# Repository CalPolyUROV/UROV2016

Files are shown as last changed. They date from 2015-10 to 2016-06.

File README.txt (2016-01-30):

# UROV_2016 README
#
##################################
#	Useful Links
##################################
#
# Arduino PWM HOW TO
#	https://www.arduino.cc/en/Tutorial/SecretsOfArduinoPWM
#
# Timer Frequency Charts 
#	https://arduino-info.wikispaces.com/Arduino-PWM-Frequency
#
# 9DOF Tutorial
# https://github.com/ptrbrtz/razor-9dof-ahrs/wiki/Tutorial
#
# TimerOne : Looks good for PWM/Periodic-Call/Call-After-Delay stuff/Call-up-to-X-times-Periodically Stuff I think
# It is driven by Interrupt as opposed to delay! (can be modified to work on other timer0/2/3/4/5) 
# https://github.com/PaulStoffregen/TimerOne
#
#
##################################
# UROV_2016 Progress
#	October 3rd- Made working prototype of rs485 communications working on Santiago
#	November 11th- Wiring diagram in Fritzing has all basic parts except DC DC converter.
#		ESCs are represented by servos because they use PWM; 12 V power to them will be implied for now. 	
#
# Vector Drive!!!
#
#Note: calling delay() in a constructor that is before the void setup will freeze the arduino
#
###BrownOut Ideas Jan16/2016 Sat, Two Ideas
#1)Use a Fractional Constant, with largest slope for x y z r
#   Possibly logrithmic
#2)Have CurrentState of Motor and Input
#   Compare, if difference too high
#     Check Time since last change of CurrentState
#       If too time too low, don't change
#       If passed minimum time margin, change CurrentState by a small amount
#         Therefore speed change is limited to SmallAmount/MinimumTimeMargin
#   Send CurrentState to Motor
#
### Brownout reality Jan23/2016
# 1) check if indivitual motor change is above a constant, now 20.
# 2) if the step is too high, only increment the motor speed by the constant (now 20)
#
#

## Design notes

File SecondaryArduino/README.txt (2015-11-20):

This holds the secondary Arduino Stuff

SerialPortDemo:
Master sends various writes and commands and requests to Slave.
Includes commands for pressure(1), temp10(2), depth(3), 1234dummy(default)

Two Commands for master:
Master Write: Call a function on Slave and set what Request returns.
    Takes 5 digit int, adds 10000(placeholder 1) converts to string and then array of characters.
    Sends array of characters one at a time.
        Slave receives array of characters, appends to a wiped string. Converts string to int and subtracts 10000.
        Stored as 5 digit int, EventCode.
            Depending on EventCode, Slave calls a function (updatePressure, runMotorMaybe?, callibrateSomething)
Master Request: Slave sends data to Master depending on EventCode
    Sends request to slave for 5 bytes of data.
        Slave decides what to data to send from most EventCode (Most Recent Input). 
            (If most recent = update Pressure, send Pressure)
        Slave takes data to be sent (int), adds 10000(placeholder 1) converts to string and then array of characters.
        Slave sends array of characters one at a time.
    Master Receives 5 characters, appends to a wiped string. Converts string to int and subtracts 10000.
    The int is the final Received Data.
    
Limitations:
    Event Code and Return Data limit is 0 to 20000 or so.
        This can likely be improved by sending data for a long or unsigned or something.
  
Problems Encountered Logs:
    Constructors cannot call delay(###). It will freeze the arduino.
        Resolved
    I2C can only pass char arrays. It cannot pass ints or strings. 
        Resolved. Lots of fun conversions, and placeholder in highest place to send an exact number of bytes.

Stuff:
1) I2C communcations. This arduino uno is slave to the primary mega
    Plan:
      Let me know if there is a better way
      a)Call a measurement / Any function
            Master uses "Wire.write(eventCode)"
            Slave has "Wire.onReceive(receiveEvent)", receiveEvent recieves eventCode and holds a Case statement
          Slave Recieves Event Code. Case statement after recieve decides what function(s) to execute
      b)Read Data
            Master uses "Wire.read()"
            Slave has "Wire.onRequest(requestEvent)", requestEvent holds a Case statement
          Slave Sends data to Master based on MOST RECENT Event Code.
            eg. 
              1) Wire.write(temperatureCode);
              2) Wire.read(); //Slave will send temperature data to Master
2) Pressure      (Nov7)
    Updated to Run On Timer One (Because Timer five  does not exist on Uno, nor does pin 45)
    Pins for Uno
        MOSI:   11
        MISO:   12
        SCK:    13
        MCLK:   10   timer1
    Sets Clock Divisor of Timer One to 1 (mode 1)
      Giving AnalogWrite 10 frequency of 32kHz
3) Accelerometer (Nov7)
    I have not looked to see if any pins need updating yet

successful test Serial Port
Start
1write
req
14701fin
2write
req
293fin
3write
req
135fin
4write
req
1030fin
End
End

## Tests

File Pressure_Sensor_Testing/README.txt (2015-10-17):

# UROV_2016 Progress
#	Put any info you find about the sensors here. Thanks!
#	-Andrew Hostler
#
#
#
#This is in case I wake up late tomorrow
#So after playing with the values in the hardcoded pressure sensor I noticed that we can't hardcode words1-4, we have to pull 
the values out of the factory calibration from the sensor (refer to pg 13 in the data sheet). If someone could explain the
diagrams on pg 13/14, that would be great. 
-Jason Mar
#
#
#
#
#
#
#
#

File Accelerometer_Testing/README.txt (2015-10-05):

# UROV_2016 Progress
#	Put any info you find about the sensors here. Thanks!
#	-Andrew Hostler
#
#
#
#
#
#
#
#
#
#
#
#
#
#

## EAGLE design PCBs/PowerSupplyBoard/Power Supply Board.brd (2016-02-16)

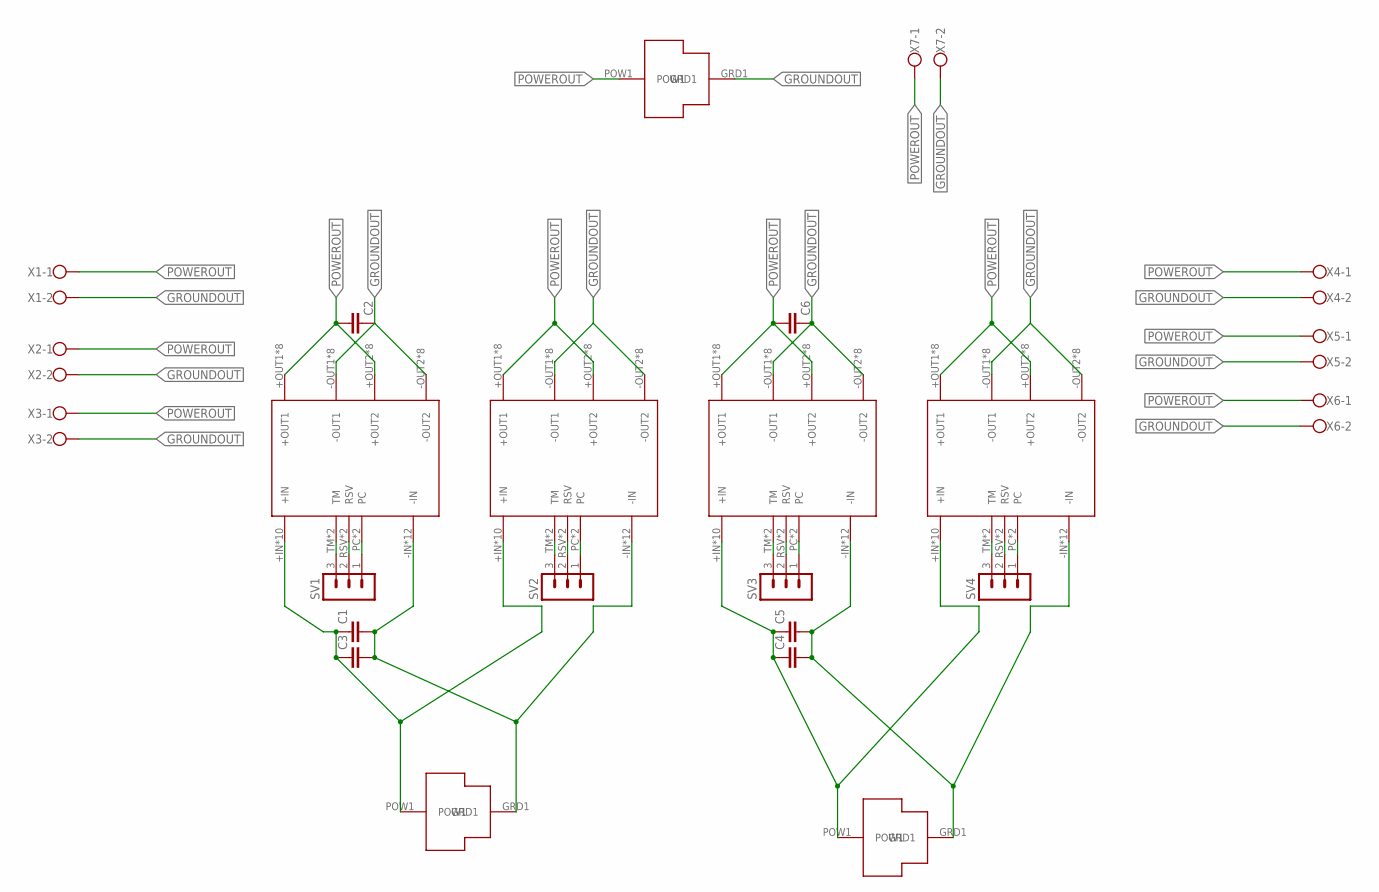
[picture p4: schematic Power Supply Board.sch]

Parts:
C1, C2, C3, C4, C5, C6: C2,5-3; C2.5-3
SV1, SV2, SV3, SV4: MA03-1
U$2, U$3, U$9: MOLEXMEGAFIT
VC1, VC2, VC3, VC4: VOLTAGECONVERTER
X1, X2, X3, X4, X5, X6, X7: W237-102

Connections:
GROUNDIN: C1.2, C3.2, C4.2, C5.2, U$3.GRD1, U$9.GRD1, VC1.-IN, VC1.-IN@0 (-IN), VC1.-IN@1 (-IN), VC1.-IN@2 (-IN), VC1.-IN@3 (-IN), VC1.-IN@4 (-IN), VC1.-IN@5 (-IN), VC1.-IN@6 (-IN), VC1.-IN@7 (-IN), VC1.-IN@8 (-IN), VC1.-IN@9 (-IN), VC1.-IN@10 (-IN), VC2.-IN, VC2.-IN@0 (-IN), VC2.-IN@1 (-IN), VC2.-IN@2 (-IN), VC2.-IN@3 (-IN), VC2.-IN@4 (-IN), VC2.-IN@5 (-IN), VC2.-IN@6 (-IN), VC2.-IN@7 (-IN), VC2.-IN@8 (-IN), VC2.-IN@9 (-IN), VC2.-IN@10 (-IN), VC3.-IN, VC3.-IN@0 (-IN), VC3.-IN@1 (-IN), VC3.-IN@2 (-IN), VC3.-IN@3 (-IN), VC3.-IN@4 (-IN), VC3.-IN@5 (-IN), VC3.-IN@6 (-IN), VC3.-IN@7 (-IN), VC3.-IN@8 (-IN), VC3.-IN@9 (-IN), VC3.-IN@10 (-IN), VC4.-IN, VC4.-IN@0 (-IN), VC4.-IN@1 (-IN), VC4.-IN@2 (-IN), VC4.-IN@3 (-IN), VC4.-IN@4 (-IN), VC4.-IN@5 (-IN), VC4.-IN@6 (-IN), VC4.-IN@7 (-IN), VC4.-IN@8 (-IN), VC4.-IN@9 (-IN), VC4.-IN@10 (-IN)
GROUNDOUT: C2.1, C6.1, U$2.GRD1, VC1.-OUT1, VC1.-OUT1@1 (-OUT1), VC1.-OUT1@2 (-OUT1), VC1.-OUT1@3 (-OUT1), VC1.-OUT1@4 (-OUT1), VC1.-OUT1@5 (-OUT1), VC1.-OUT1@6 (-OUT1), VC1.-OUT1@7 (-OUT1), VC1.-OUT2, VC1.-OUT2@1 (-OUT2), VC1.-OUT2@2 (-OUT2), VC1.-OUT2@3 (-OUT2), VC1.-OUT2@4 (-OUT2), VC1.-OUT2@5 (-OUT2), VC1.-OUT2@6 (-OUT2), VC1.-OUT2@7 (-OUT2), VC2.-OUT1, VC2.-OUT1@1 (-OUT1), VC2.-OUT1@2 (-OUT1), VC2.-OUT1@3 (-OUT1), VC2.-OUT1@4 (-OUT1), VC2.-OUT1@5 (-OUT1), VC2.-OUT1@6 (-OUT1), VC2.-OUT1@7 (-OUT1), VC2.-OUT2, VC2.-OUT2@1 (-OUT2), VC2.-OUT2@2 (-OUT2), VC2.-OUT2@3 (-OUT2), VC2.-OUT2@4 (-OUT2), VC2.-OUT2@5 (-OUT2), VC2.-OUT2@6 (-OUT2), VC2.-OUT2@7 (-OUT2), VC3.-OUT1, VC3.-OUT1@1 (-OUT1), VC3.-OUT1@2 (-OUT1), VC3.-OUT1@3 (-OUT1), VC3.-OUT1@4 (-OUT1), VC3.-OUT1@5 (-OUT1), VC3.-OUT1@6 (-OUT1), VC3.-OUT1@7 (-OUT1), VC3.-OUT2, VC3.-OUT2@1 (-OUT2), VC3.-OUT2@2 (-OUT2), VC3.-OUT2@3 (-OUT2), VC3.-OUT2@4 (-OUT2), VC3.-OUT2@5 (-OUT2), VC3.-OUT2@6 (-OUT2), VC3.-OUT2@7 (-OUT2), VC4.-OUT1, VC4.-OUT1@1 (-OUT1), VC4.-OUT1@2 (-OUT1), VC4.-OUT1@3 (-OUT1), VC4.-OUT1@4 (-OUT1), VC4.-OUT1@5 (-OUT1), VC4.-OUT1@6 (-OUT1), VC4.-OUT1@7 (-OUT1), VC4.-OUT2, VC4.-OUT2@1 (-OUT2), VC4.-OUT2@2 (-OUT2), VC4.-OUT2@3 (-OUT2), VC4.-OUT2@4 (-OUT2), VC4.-OUT2@5 (-OUT2), VC4.-OUT2@6 (-OUT2), VC4.-OUT2@7 (-OUT2), X1.2, X2.2, X3.2, X4.2, X5.2, X6.2, X7.2
unnamed: SV1.3, VC1.TM, VC1.TM@1 (TM)
unnamed: SV1.2, VC1.RSV, VC1.RSV@1 (RSV)
unnamed: SV1.1, VC1.PC, VC1.PC21 (PC)
unnamed: SV2.3, VC2.TM, VC2.TM@1 (TM)
unnamed: SV2.2, VC2.RSV, VC2.RSV@1 (RSV)
unnamed: SV2.1, VC2.PC, VC2.PC21 (PC)
unnamed: SV3.3, VC3.TM, VC3.TM@1 (TM)
unnamed: SV3.2, VC3.RSV, VC3.RSV@1 (RSV)
unnamed: SV3.1, VC3.PC, VC3.PC21 (PC)
unnamed: SV4.3, VC4.TM, VC4.TM@1 (TM)
unnamed: SV4.2, VC4.RSV, VC4.RSV@1 (RSV)
unnamed: SV4.1, VC4.PC, VC4.PC21 (PC)
POWERIN12: C1.1, C3.1, U$3.POW1, VC1.+IN, VC1.+IN@1 (+IN), VC1.+IN@2 (+IN), VC1.+IN@3 (+IN), VC1.+IN@4 (+IN), VC1.+IN@5 (+IN), VC1.+IN@6 (+IN), VC1.+IN@7 (+IN), VC1.+IN@8 (+IN), VC1.+IN@9 (+IN), VC2.+IN, VC2.+IN@1 (+IN), VC2.+IN@2 (+IN), VC2.+IN@3 (+IN), VC2.+IN@4 (+IN), VC2.+IN@5 (+IN), VC2.+IN@6 (+IN), VC2.+IN@7 (+IN), VC2.+IN@8 (+IN), VC2.+IN@9 (+IN)
POWERIN34: C4.1, C5.1, U$9.POW1, VC3.+IN, VC3.+IN@1 (+IN), VC3.+IN@2 (+IN), VC3.+IN@3 (+IN), VC3.+IN@4 (+IN), VC3.+IN@5 (+IN), VC3.+IN@6 (+IN), VC3.+IN@7 (+IN), VC3.+IN@8 (+IN), VC3.+IN@9 (+IN), VC4.+IN, VC4.+IN@1 (+IN), VC4.+IN@2 (+IN), VC4.+IN@3 (+IN), VC4.+IN@4 (+IN), VC4.+IN@5 (+IN), VC4.+IN@6 (+IN), VC4.+IN@7 (+IN), VC4.+IN@8 (+IN), VC4.+IN@9 (+IN)
POWEROUT: C2.2, C6.2, U$2.POW1, VC1.+OUT1, VC1.+OUT1@1 (+OUT1), VC1.+OUT1@2 (+OUT1), VC1.+OUT1@3 (+OUT1), VC1.+OUT1@4 (+OUT1), VC1.+OUT1@5 (+OUT1), VC1.+OUT1@6 (+OUT1), VC1.+OUT1@7 (+OUT1), VC1.+OUT2, VC1.+OUT2@1 (+OUT2), VC1.+OUT2@2 (+OUT2), VC1.+OUT2@3 (+OUT2), VC1.+OUT2@4 (+OUT2), VC1.+OUT2@5 (+OUT2), VC1.+OUT2@6 (+OUT2), VC1.+OUT2@7 (+OUT2), VC2.+OUT1, VC2.+OUT1@1 (+OUT1), VC2.+OUT1@2 (+OUT1), VC2.+OUT1@3 (+OUT1), VC2.+OUT1@4 (+OUT1), VC2.+OUT1@5 (+OUT1), VC2.+OUT1@6 (+OUT1), VC2.+OUT1@7 (+OUT1), VC2.+OUT2, VC2.+OUT2@1 (+OUT2), VC2.+OUT2@2 (+OUT2), VC2.+OUT2@3 (+OUT2), VC2.+OUT2@4 (+OUT2), VC2.+OUT2@5 (+OUT2), VC2.+OUT2@6 (+OUT2), VC2.+OUT2@7 (+OUT2), VC3.+OUT1, VC3.+OUT1@1 (+OUT1), VC3.+OUT1@2 (+OUT1), VC3.+OUT1@3 (+OUT1), VC3.+OUT1@4 (+OUT1), VC3.+OUT1@5 (+OUT1), VC3.+OUT1@6 (+OUT1), VC3.+OUT1@7 (+OUT1), VC3.+OUT2, VC3.+OUT2@1 (+OUT2), VC3.+OUT2@2 (+OUT2), VC3.+OUT2@3 (+OUT2), VC3.+OUT2@4 (+OUT2), VC3.+OUT2@5 (+OUT2), VC3.+OUT2@6 (+OUT2), VC3.+OUT2@7 (+OUT2), VC4.+OUT1, VC4.+OUT1@1 (+OUT1), VC4.+OUT1@2 (+OUT1), VC4.+OUT1@3 (+OUT1), VC4.+OUT1@4 (+OUT1), VC4.+OUT1@5 (+OUT1), VC4.+OUT1@6 (+OUT1), VC4.+OUT1@7 (+OUT1), VC4.+OUT2, VC4.+OUT2@1 (+OUT2), VC4.+OUT2@2 (+OUT2), VC4.+OUT2@3 (+OUT2), VC4.+OUT2@4 (+OUT2), VC4.+OUT2@5 (+OUT2), VC4.+OUT2@6 (+OUT2), VC4.+OUT2@7 (+OUT2), X1.1, X2.1, X3.1, X4.1, X5.1, X6.1, X7.1

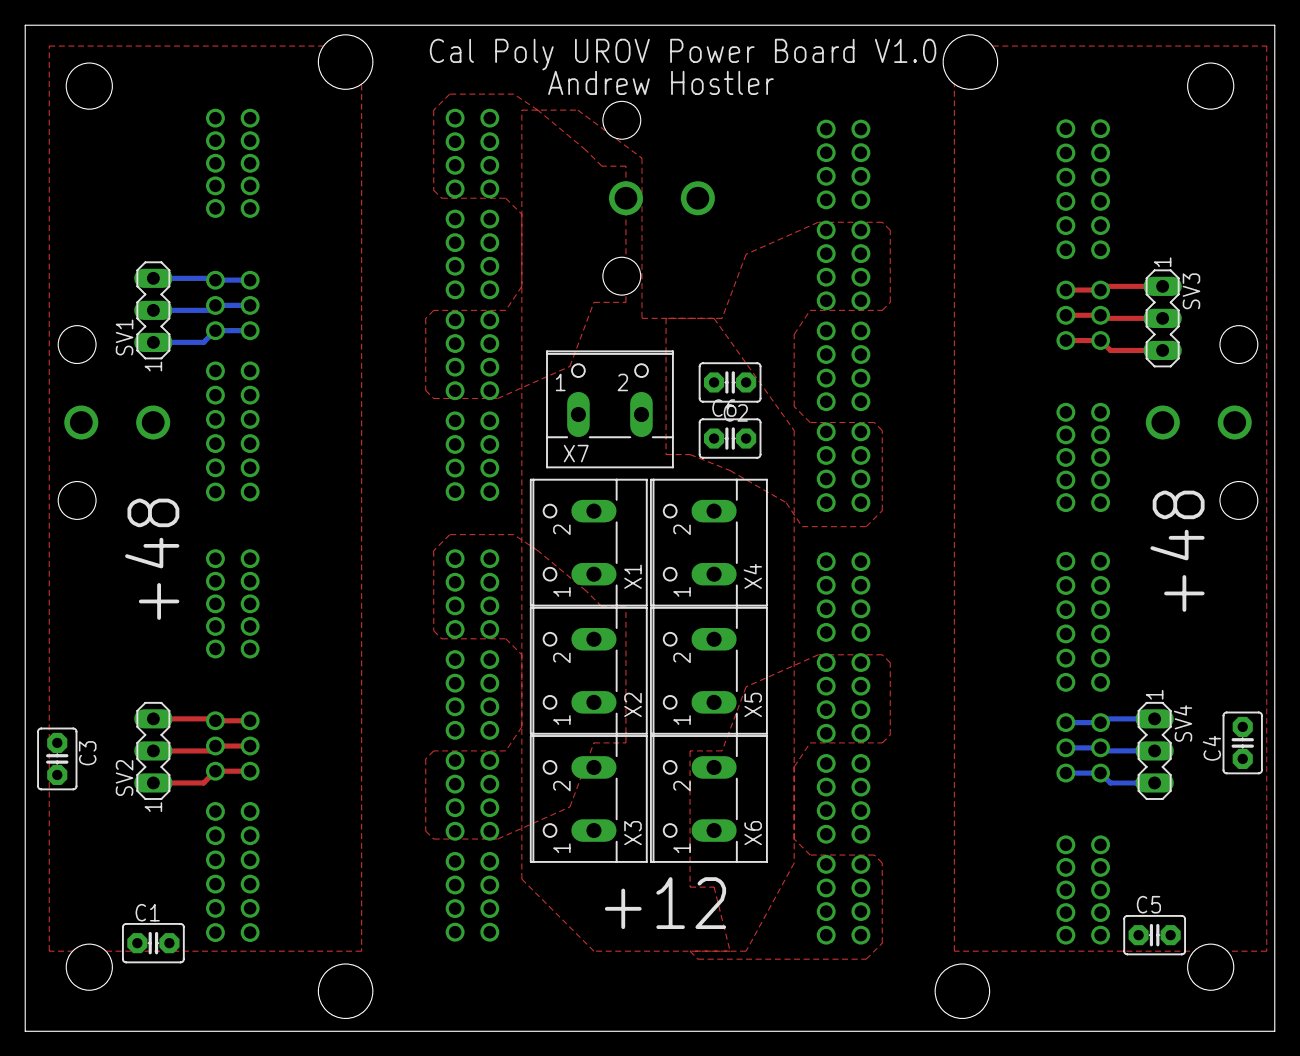
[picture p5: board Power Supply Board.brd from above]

Board: 2 copper layers, 99.1 x 79.8 mm, 24 parts (0 on the bottom side), 17 nets.

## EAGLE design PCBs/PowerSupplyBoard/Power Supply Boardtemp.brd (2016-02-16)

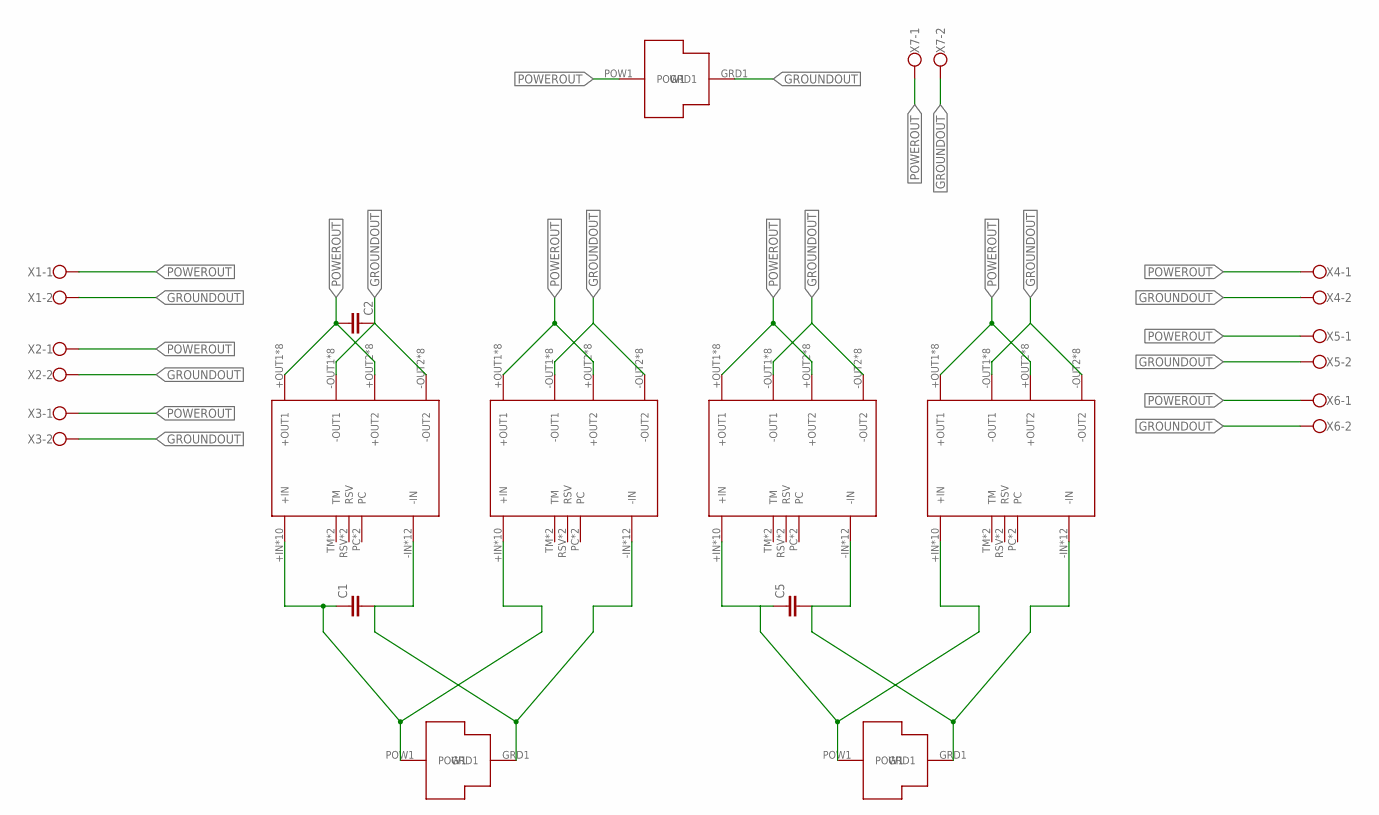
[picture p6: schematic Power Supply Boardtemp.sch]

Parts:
C1, C2, C5: C2,5-3; C2.5-3
U$2, U$3, U$9: MOLEXMEGAFIT
VC1, VC2, VC3, VC4: VOLTAGECONVERTER
X1, X2, X3, X4, X5, X6, X7: W237-102

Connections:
GROUNDIN: C1.2, C5.2, U$3.GRD1, U$9.GRD1, VC1.-IN, VC1.-IN@0 (-IN), VC1.-IN@1 (-IN), VC1.-IN@2 (-IN), VC1.-IN@3 (-IN), VC1.-IN@4 (-IN), VC1.-IN@5 (-IN), VC1.-IN@6 (-IN), VC1.-IN@7 (-IN), VC1.-IN@8 (-IN), VC1.-IN@9 (-IN), VC1.-IN@10 (-IN), VC2.-IN, VC2.-IN@0 (-IN), VC2.-IN@1 (-IN), VC2.-IN@2 (-IN), VC2.-IN@3 (-IN), VC2.-IN@4 (-IN), VC2.-IN@5 (-IN), VC2.-IN@6 (-IN), VC2.-IN@7 (-IN), VC2.-IN@8 (-IN), VC2.-IN@9 (-IN), VC2.-IN@10 (-IN), VC3.-IN, VC3.-IN@0 (-IN), VC3.-IN@1 (-IN), VC3.-IN@2 (-IN), VC3.-IN@3 (-IN), VC3.-IN@4 (-IN), VC3.-IN@5 (-IN), VC3.-IN@6 (-IN), VC3.-IN@7 (-IN), VC3.-IN@8 (-IN), VC3.-IN@9 (-IN), VC3.-IN@10 (-IN), VC4.-IN, VC4.-IN@0 (-IN), VC4.-IN@1 (-IN), VC4.-IN@2 (-IN), VC4.-IN@3 (-IN), VC4.-IN@4 (-IN), VC4.-IN@5 (-IN), VC4.-IN@6 (-IN), VC4.-IN@7 (-IN), VC4.-IN@8 (-IN), VC4.-IN@9 (-IN), VC4.-IN@10 (-IN)
GROUNDOUT: C2.1, U$2.GRD1, VC1.-OUT1, VC1.-OUT1@1 (-OUT1), VC1.-OUT1@2 (-OUT1), VC1.-OUT1@3 (-OUT1), VC1.-OUT1@4 (-OUT1), VC1.-OUT1@5 (-OUT1), VC1.-OUT1@6 (-OUT1), VC1.-OUT1@7 (-OUT1), VC1.-OUT2, VC1.-OUT2@1 (-OUT2), VC1.-OUT2@2 (-OUT2), VC1.-OUT2@3 (-OUT2), VC1.-OUT2@4 (-OUT2), VC1.-OUT2@5 (-OUT2), VC1.-OUT2@6 (-OUT2), VC1.-OUT2@7 (-OUT2), VC2.-OUT1, VC2.-OUT1@1 (-OUT1), VC2.-OUT1@2 (-OUT1), VC2.-OUT1@3 (-OUT1), VC2.-OUT1@4 (-OUT1), VC2.-OUT1@5 (-OUT1), VC2.-OUT1@6 (-OUT1), VC2.-OUT1@7 (-OUT1), VC2.-OUT2, VC2.-OUT2@1 (-OUT2), VC2.-OUT2@2 (-OUT2), VC2.-OUT2@3 (-OUT2), VC2.-OUT2@4 (-OUT2), VC2.-OUT2@5 (-OUT2), VC2.-OUT2@6 (-OUT2), VC2.-OUT2@7 (-OUT2), VC3.-OUT1, VC3.-OUT1@1 (-OUT1), VC3.-OUT1@2 (-OUT1), VC3.-OUT1@3 (-OUT1), VC3.-OUT1@4 (-OUT1), VC3.-OUT1@5 (-OUT1), VC3.-OUT1@6 (-OUT1), VC3.-OUT1@7 (-OUT1), VC3.-OUT2, VC3.-OUT2@1 (-OUT2), VC3.-OUT2@2 (-OUT2), VC3.-OUT2@3 (-OUT2), VC3.-OUT2@4 (-OUT2), VC3.-OUT2@5 (-OUT2), VC3.-OUT2@6 (-OUT2), VC3.-OUT2@7 (-OUT2), VC4.-OUT1, VC4.-OUT1@1 (-OUT1), VC4.-OUT1@2 (-OUT1), VC4.-OUT1@3 (-OUT1), VC4.-OUT1@4 (-OUT1), VC4.-OUT1@5 (-OUT1), VC4.-OUT1@6 (-OUT1), VC4.-OUT1@7 (-OUT1), VC4.-OUT2, VC4.-OUT2@1 (-OUT2), VC4.-OUT2@2 (-OUT2), VC4.-OUT2@3 (-OUT2), VC4.-OUT2@4 (-OUT2), VC4.-OUT2@5 (-OUT2), VC4.-OUT2@6 (-OUT2), VC4.-OUT2@7 (-OUT2), X1.2, X2.2, X3.2, X4.2, X5.2, X6.2, X7.2
POWERIN12: C1.1, U$3.POW1, VC1.+IN, VC1.+IN@1 (+IN), VC1.+IN@2 (+IN), VC1.+IN@3 (+IN), VC1.+IN@4 (+IN), VC1.+IN@5 (+IN), VC1.+IN@6 (+IN), VC1.+IN@7 (+IN), VC1.+IN@8 (+IN), VC1.+IN@9 (+IN), VC2.+IN, VC2.+IN@1 (+IN), VC2.+IN@2 (+IN), VC2.+IN@3 (+IN), VC2.+IN@4 (+IN), VC2.+IN@5 (+IN), VC2.+IN@6 (+IN), VC2.+IN@7 (+IN), VC2.+IN@8 (+IN), VC2.+IN@9 (+IN)
POWERIN34: C5.1, U$9.POW1, VC3.+IN, VC3.+IN@1 (+IN), VC3.+IN@2 (+IN), VC3.+IN@3 (+IN), VC3.+IN@4 (+IN), VC3.+IN@5 (+IN), VC3.+IN@6 (+IN), VC3.+IN@7 (+IN), VC3.+IN@8 (+IN), VC3.+IN@9 (+IN), VC4.+IN, VC4.+IN@1 (+IN), VC4.+IN@2 (+IN), VC4.+IN@3 (+IN), VC4.+IN@4 (+IN), VC4.+IN@5 (+IN), VC4.+IN@6 (+IN), VC4.+IN@7 (+IN), VC4.+IN@8 (+IN), VC4.+IN@9 (+IN)
POWEROUT: C2.2, U$2.POW1, VC1.+OUT1, VC1.+OUT1@1 (+OUT1), VC1.+OUT1@2 (+OUT1), VC1.+OUT1@3 (+OUT1), VC1.+OUT1@4 (+OUT1), VC1.+OUT1@5 (+OUT1), VC1.+OUT1@6 (+OUT1), VC1.+OUT1@7 (+OUT1), VC1.+OUT2, VC1.+OUT2@1 (+OUT2), VC1.+OUT2@2 (+OUT2), VC1.+OUT2@3 (+OUT2), VC1.+OUT2@4 (+OUT2), VC1.+OUT2@5 (+OUT2), VC1.+OUT2@6 (+OUT2), VC1.+OUT2@7 (+OUT2), VC2.+OUT1, VC2.+OUT1@1 (+OUT1), VC2.+OUT1@2 (+OUT1), VC2.+OUT1@3 (+OUT1), VC2.+OUT1@4 (+OUT1), VC2.+OUT1@5 (+OUT1), VC2.+OUT1@6 (+OUT1), VC2.+OUT1@7 (+OUT1), VC2.+OUT2, VC2.+OUT2@1 (+OUT2), VC2.+OUT2@2 (+OUT2), VC2.+OUT2@3 (+OUT2), VC2.+OUT2@4 (+OUT2), VC2.+OUT2@5 (+OUT2), VC2.+OUT2@6 (+OUT2), VC2.+OUT2@7 (+OUT2), VC3.+OUT1, VC3.+OUT1@1 (+OUT1), VC3.+OUT1@2 (+OUT1), VC3.+OUT1@3 (+OUT1), VC3.+OUT1@4 (+OUT1), VC3.+OUT1@5 (+OUT1), VC3.+OUT1@6 (+OUT1), VC3.+OUT1@7 (+OUT1), VC3.+OUT2, VC3.+OUT2@1 (+OUT2), VC3.+OUT2@2 (+OUT2), VC3.+OUT2@3 (+OUT2), VC3.+OUT2@4 (+OUT2), VC3.+OUT2@5 (+OUT2), VC3.+OUT2@6 (+OUT2), VC3.+OUT2@7 (+OUT2), VC4.+OUT1, VC4.+OUT1@1 (+OUT1), VC4.+OUT1@2 (+OUT1), VC4.+OUT1@3 (+OUT1), VC4.+OUT1@4 (+OUT1), VC4.+OUT1@5 (+OUT1), VC4.+OUT1@6 (+OUT1), VC4.+OUT1@7 (+OUT1), VC4.+OUT2, VC4.+OUT2@1 (+OUT2), VC4.+OUT2@2 (+OUT2), VC4.+OUT2@3 (+OUT2), VC4.+OUT2@4 (+OUT2), VC4.+OUT2@5 (+OUT2), VC4.+OUT2@6 (+OUT2), VC4.+OUT2@7 (+OUT2), X1.1, X2.1, X3.1, X4.1, X5.1, X6.1, X7.1

Board: 2 copper layers, 24 parts (0 on the bottom side), 5 nets, no tracks yet.

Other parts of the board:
E$1, E$2, E$3, E$4, E$5, E$6, E$7: W237-102

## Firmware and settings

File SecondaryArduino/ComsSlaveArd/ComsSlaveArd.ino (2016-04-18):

#define GET_TEMP 1
#define GET_PRES 2
#define GET_DEPT 3
#define GET_YAW  4
#define GET_PCH 5
#define GET_ROL 6


/***************************************************************************************************************
* Razor AHRS Firmware v1.4.2
* 9 Degree of Measurement Attitude and Heading Reference System
* for Sparkfun "9DOF Razor IMU" (SEN-10125 and SEN-10736)
* and "9DOF Sensor Stick" (SEN-10183, 10321 and SEN-10724)
*
* Released under GNU GPL (General Public License) v3.0
* Copyright (C) 2013 Peter Bartz [http://ptrbrtz.net]
* Copyright (C) 2011-2012 Quality & Usability Lab, Deutsche Telekom Laboratories, TU Berlin
*
* Infos, updates, bug reports, contributions and feedback:
*     https://github.com/ptrbrtz/razor-9dof-ahrs
*
*
* History:
*   * Original code (http://code.google.com/p/sf9domahrs/) by Doug Weibel and Jose Julio,
*     based on ArduIMU v1.5 by Jordi Munoz and William Premerlani, Jose Julio and Doug Weibel. Thank you!
*
*   * Updated code (http://groups.google.com/group/sf_9dof_ahrs_update) by David Malik (david.zsolt.malik@gmail.com)
*     for new Sparkfun 9DOF Razor hardware (SEN-10125).
*
*   * Updated and extended by Peter Bartz (peter-bartz@gmx.de):
*     * v1.3.0
*       * Cleaned up, streamlined and restructured most of the code to make it more comprehensible.
*       * Added sensor calibration (improves precision and responsiveness a lot!).
*       * Added binary yaw/pitch/roll output.
*       * Added basic serial command interface to set output modes/calibrate sensors/synch stream/etc.
*       * Added support to synch automatically when using Rovering Networks Bluetooth modules (and compatible).
*       * Wrote new easier to use test program (using Processing).
*       * Added support for new version of "9DOF Razor IMU": SEN-10736.
*       --> The output of this code is not compatible with the older versions!
*       --> A Processing sketch to test the tracker is available.
*     * v1.3.1
*       * Initializing rotation matrix based on start-up sensor readings -> orientation OK right away.
*       * Adjusted gyro low-pass filter and output rate settings.
*     * v1.3.2
*       * Adapted code to work with new Arduino 1.0 (and older versions still).
*     * v1.3.3
*       * Improved synching.
*     * v1.4.0
*       * Added support for SparkFun "9DOF Sensor Stick" (versions SEN-10183, SEN-10321 and SEN-10724).
*     * v1.4.1
*       * Added output modes to read raw and/or calibrated sensor data in text or binary format.
*       * Added static magnetometer soft iron distortion compensation
*     * v1.4.2
*       * (No core firmware changes)
*
* TODOs:
*   * Allow optional use of EEPROM for storing and reading calibration values.
*   * Use self-test and temperature-compensation features of the sensors.
***************************************************************************************************************/

/*
  "9DOF Razor IMU" hardware versions: SEN-10125 and SEN-10736

  ATMega328@3.3V, 8MHz

  ADXL345  : Accelerometer
  HMC5843  : Magnetometer on SEN-10125
  HMC5883L : Magnetometer on SEN-10736
  ITG-3200 : Gyro

  Arduino IDE : Select board "Arduino Pro or Pro Mini (3.3v, 8Mhz) w/ATmega328"
*/

/*
  "9DOF Sensor Stick" hardware versions: SEN-10183, SEN-10321 and SEN-10724

  ADXL345  : Accelerometer
  HMC5843  : Magnetometer on SEN-10183 and SEN-10321
  HMC5883L : Magnetometer on SEN-10724
  ITG-3200 : Gyro
*/

/*
  Axis definition (differs from definition printed on the board!):
    X axis pointing forward (towards the short edge with the connector holes)
    Y axis pointing to the right
    and Z axis pointing down.
    
  Positive yaw   : clockwise
  Positive roll  : right wing down
  Positive pitch : nose up
  
  Transformation order: first yaw then pitch then roll.
*/

/*
  Serial commands that the firmware understands:
  
  "#o<params>" - Set OUTPUT mode and parameters. The available options are:
  
      // Streaming output
      "#o0" - DISABLE continuous streaming output. Also see #f below.
      "#o1" - ENABLE continuous streaming output.
      
      // Angles output
      "#ob" - Output angles in BINARY format (yaw/pitch/roll as binary float, so one output frame
              is 3x4 = 12 bytes long).
      "#ot" - Output angles in TEXT format (Output frames have form like "#YPR=-142.28,-5.38,33.52",
              followed by carriage return and line feed [\r\n]).
      
      // Sensor calibration
      "#oc" - Go to CALIBRATION output mode.
      "#on" - When in calibration mode, go on to calibrate NEXT sensor.
      
      // Sensor data output
      "#osct" - Output CALIBRATED SENSOR data of all 9 axes in TEXT format.
                One frame consist of three lines - one for each sensor: acc, mag, gyr.
      "#osrt" - Output RAW SENSOR data of all 9 axes in TEXT format.
                One frame consist of three lines - one for each sensor: acc, mag, gyr.
      "#osbt" - Output BOTH raw and calibrated SENSOR data of all 9 axes in TEXT format.
                One frame consist of six lines - like #osrt and #osct combined (first RAW, then CALIBRATED).
                NOTE: This is a lot of number-to-text conversion work for the little 8MHz chip on the Razor boards.
                In fact it's too much and an output frame rate of 50Hz can not be maintained. #osbb.
      "#oscb" - Output CALIBRATED SENSOR data of all 9 axes in BINARY format.
                One frame consist of three 3x3 float values = 36 bytes. Order is: acc x/y/z, mag x/y/z, gyr x/y/z.
      "#osrb" - Output RAW SENSOR data of all 9 axes in BINARY format.
                One frame consist of three 3x3 float values = 36 bytes. Order is: acc x/y/z, mag x/y/z, gyr x/y/z.
      "#osbb" - Output BOTH raw and calibrated SENSOR data of all 9 axes in BINARY format.
                One frame consist of 2x36 = 72 bytes - like #osrb and #oscb combined (first RAW, then CALIBRATED).
      
      // Error message output        
      "#oe0" - Disable ERROR message output.
      "#oe1" - Enable ERROR message output.
    
    
  "#f" - Request one output frame - useful when continuous output is disabled and updates are
         required in larger intervals only. Though #f only requests one reply, replies are still
         bound to the internal 20ms (50Hz) time raster. So worst case delay that #f can add is 19.99ms.
         
         
  "#s<xy>" - Request synch token - useful to find out where the frame boundaries are in a continuous
         binary stream or to see if tracker is present and answering. The tracker will send
         "#SYNCH<xy>\r\n" in response (so it's possible to read using a readLine() function).
         x and y are two mandatory but arbitrary bytes that can be used to find out which request
         the answer belongs to.
          
          
  ("#C" and "#D" - Reserved for communication with optional Bluetooth module.)
  
  Newline characters are not required. So you could send "#ob#o1#s", which
  would set binary output mode, enable continuous streaming output and request
  a synch token all at once.
  
  The status LED will be on if streaming output is enabled and off otherwise.
  
  Byte order of binary output is little-endian: least significant byte comes first.
*/



/*****************************************************************/
/*********** USER SETUP AREA! Set your options here! *************/
/*****************************************************************/

// HARDWARE OPTIONS
/*****************************************************************/
// Select your hardware here by uncommenting one line!
//#define HW__VERSION_CODE 10125 // SparkFun "9DOF Razor IMU" version "SEN-10125" (HMC5843 magnetometer)
//#define HW__VERSION_CODE 10736 // SparkFun "9DOF Razor IMU" version "SEN-10736" (HMC5883L magnetometer)
#define HW__VERSION_CODE 10183 // SparkFun "9DOF Sensor Stick" version "SEN-10183" (HMC5843 magnetometer)
//#define HW__VERSION_CODE 10321 // SparkFun "9DOF Sensor Stick" version "SEN-10321" (HMC5843 magnetometer)
//#define HW__VERSION_CODE 10724 // SparkFun "9DOF Sensor Stick" version "SEN-10724" (HMC5883L magnetometer)


// OUTPUT OPTIONS
/*****************************************************************/
// Set your serial port baud rate used to send out data here!
//#define OUTPUT__BAUD_RATE 57600 // Old
#define OUTPUT__BAUD_RATE 9600
// Sensor data output interval in milliseconds
// This may not work, if faster than 20ms (=50Hz)
// Code is tuned for 20ms, so better leave it like that
#define OUTPUT__DATA_INTERVAL 100  // in milliseconds

// Output mode definitions (do not change)
#define OUTPUT__MODE_CALIBRATE_SENSORS 0 // Outputs sensor min/max values as text for manual calibration
#define OUTPUT__MODE_ANGLES 1 // Outputs yaw/pitch/roll in degrees
#define OUTPUT__MODE_SENSORS_CALIB 2 // Outputs calibrated sensor values for all 9 axes
#define OUTPUT__MODE_SENSORS_RAW 3 // Outputs raw (uncalibrated) sensor values for all 9 axes
#define OUTPUT__MODE_SENSORS_BOTH 4 // Outputs calibrated AND raw sensor values for all 9 axes
// Output format definitions (do not change)
#define OUTPUT__FORMAT_TEXT 0 // Outputs data as text
#define OUTPUT__FORMAT_BINARY 1 // Outputs data as binary float

// Select your startup output mode and format here!
int output_mode = OUTPUT__MODE_ANGLES;
int output_format = OUTPUT__FORMAT_TEXT;

// Select if serial continuous streaming output is enabled per default on startup.
#define OUTPUT__STARTUP_STREAM_ON true  // true or false

// If set true, an error message will be output if we fail to read sensor data.
// Message format: "!ERR: reading <sensor>", followed by "\r\n".
boolean output_errors = false;  // true or false

// Bluetooth
// You can set this to true, if you have a Rovering Networks Bluetooth Module attached.
// The connect/disconnect message prefix of the module has to be set to "#".
// (Refer to manual, it can be set like this: SO,#)
// When using this, streaming output will only be enabled as long as we're connected. That way
// receiver and sender are synchronzed easily just by connecting/disconnecting.
// It is not necessary to set this! It just makes life easier when writing code for
// the receiving side. The Processing test sketch also works without setting this.
// NOTE: When using this, OUTPUT__STARTUP_STREAM_ON has no effect!
#define OUTPUT__HAS_RN_BLUETOOTH false  // true or false


// SENSOR CALIBRATION
/*****************************************************************/
// How to calibrate? Read the tutorial at http://dev.qu.tu-berlin.de/projects/sf-razor-9dof-ahrs
// Put MIN/MAX and OFFSET readings for your board here!
// Accelerometer
// "accel x,y,z (min/max) = X_MIN/X_MAX  Y_MIN/Y_MAX  Z_MIN/Z_MAX"
#define ACCEL_X_MIN ((float) -250)
#define ACCEL_X_MAX ((float) 250)
#define ACCEL_Y_MIN ((float) -250)
#define ACCEL_Y_MAX ((float) 250)
#define ACCEL_Z_MIN ((float) -250)
#define ACCEL_Z_MAX ((float) 250)

// Magnetometer (standard calibration mode)
// "magn x,y,z (min/max) = X_MIN/X_MAX  Y_MIN/Y_MAX  Z_MIN/Z_MAX"
#define MAGN_X_MIN ((float) -600)
#define MAGN_X_MAX ((float) 600)
#define MAGN_Y_MIN ((float) -600)
#define MAGN_Y_MAX ((float) 600)
#define MAGN_Z_MIN ((float) -600)
#define MAGN_Z_MAX ((float) 600)

// Magnetometer (extended calibration mode)
// Uncommend to use extended magnetometer calibration (compensates hard & soft iron errors)
//#define CALIBRATION__MAGN_USE_EXTENDED true
//const float magn_ellipsoid_center[3] = {0, 0, 0};
//const float magn_ellipsoid_transform[3][3] = {{0, 0, 0}, {0, 0, 0}, {0, 0, 0}};

// Gyroscope
// "gyro x,y,z (current/average) = .../OFFSET_X  .../OFFSET_Y  .../OFFSET_Z
#define GYRO_AVERAGE_OFFSET_X ((float) 0.0)
#define GYRO_AVERAGE_OFFSET_Y ((float) 0.0)
#define GYRO_AVERAGE_OFFSET_Z ((float) 0.0)

/*
// Calibration example:

// "accel x,y,z (min/max) = -277.00/264.00  -256.00/278.00  -299.00/235.00"
#define ACCEL_X_MIN ((float) -277)
#define ACCEL_X_MAX ((float) 264)
#define ACCEL_Y_MIN ((float) -256)
#define ACCEL_Y_MAX ((float) 278)
#define ACCEL_Z_MIN ((float) -299)
#define ACCEL_Z_MAX ((float) 235)

// "magn x,y,z (min/max) = -511.00/581.00  -516.00/568.00  -489.00/486.00"
//#define MAGN_X_MIN ((float) -511)
//#define MAGN_X_MAX ((float) 581)
//#define MAGN_Y_MIN ((float) -516)
//#define MAGN_Y_MAX ((float) 568)
//#define MAGN_Z_MIN ((float) -489)
//#define MAGN_Z_MAX ((float) 486)

// Extended magn
#define CALIBRATION__MAGN_USE_EXTENDED true
const float magn_ellipsoid_center[3] = {91.5, -13.5, -48.1};
const float magn_ellipsoid_transform[3][3] = {{0.902, -0.00354, 0.000636}, {-0.00354, 0.9, -0.00599}, {0.000636, -0.00599, 1}};

// Extended magn (with Sennheiser HD 485 headphones)
//#define CALIBRATION__MAGN_USE_EXTENDED true
//const float magn_ellipsoid_center[3] = {72.3360, 23.0954, 53.6261};
//const float magn_ellipsoid_transform[3][3] = {{0.879685, 0.000540833, -0.0106054}, {0.000540833, 0.891086, -0.0130338}, {-0.0106054, -0.0130338, 0.997494}};

//"gyro x,y,z (current/average) = -40.00/-42.05  98.00/96.20  -18.00/-18.36"
#define GYRO_AVERAGE_OFFSET_X ((float) -42.05)
#define GYRO_AVERAGE_OFFSET_Y ((float) 96.20)
#define GYRO_AVERAGE_OFFSET_Z ((float) -18.36)
*/


// DEBUG OPTIONS
/*****************************************************************/
// When set to true, gyro drift correction will not be applied
#define DEBUG__NO_DRIFT_CORRECTION false
// Print elapsed time after each I/O loop
#define DEBUG__PRINT_LOOP_TIME false


/*****************************************************************/
/****************** END OF USER SETUP AREA!  *********************/
/*****************************************************************/










// Check if hardware version code is defined
#ifndef HW__VERSION_CODE
  // Generate compile error
  #error YOU HAVE TO SELECT THE HARDWARE YOU ARE USING! See "HARDWARE OPTIONS" in "USER SETUP AREA" at top of Razor_AHRS.ino!
#endif

#include <Wire.h>

// Sensor calibration scale and offset values
#define ACCEL_X_OFFSET ((ACCEL_X_MIN + ACCEL_X_MAX) / 2.0f)
#define ACCEL_Y_OFFSET ((ACCEL_Y_MIN + ACCEL_Y_MAX) / 2.0f)
#define ACCEL_Z_OFFSET ((ACCEL_Z_MIN + ACCEL_Z_MAX) / 2.0f)
#define ACCEL_X_SCALE (GRAVITY / (ACCEL_X_MAX - ACCEL_X_OFFSET))
#define ACCEL_Y_SCALE (GRAVITY / (ACCEL_Y_MAX - ACCEL_Y_OFFSET))
#define ACCEL_Z_SCALE (GRAVITY / (ACCEL_Z_MAX - ACCEL_Z_OFFSET))

#define MAGN_X_OFFSET ((MAGN_X_MIN + MAGN_X_MAX) / 2.0f)
#define MAGN_Y_OFFSET ((MAGN_Y_MIN + MAGN_Y_MAX) / 2.0f)
#define MAGN_Z_OFFSET ((MAGN_Z_MIN + MAGN_Z_MAX) / 2.0f)
#define MAGN_X_SCALE (100.0f / (MAGN_X_MAX - MAGN_X_OFFSET))
#define MAGN_Y_SCALE (100.0f / (MAGN_Y_MAX - MAGN_Y_OFFSET))
#define MAGN_Z_SCALE (100.0f / (MAGN_Z_MAX - MAGN_Z_OFFSET))


// Gain for gyroscope (ITG-3200)
#define GYRO_GAIN 0.06957 // Same gain on all axes
#define GYRO_SCALED_RAD(x) (x * TO_RAD(GYRO_GAIN)) // Calculate the scaled gyro readings in radians per second

// DCM parameters
#define Kp_ROLLPITCH 0.02f
#define Ki_ROLLPITCH 0.00002f
#define Kp_YAW 1.2f
#define Ki_YAW 0.00002f

// Stuff
#define STATUS_LED_PIN 13  // Pin number of status LED
#define GRAVITY 256.0f // "1G reference" used for DCM filter and accelerometer calibration
#define TO_RAD(x) (x * 0.01745329252)  // *pi/180
#define TO_DEG(x) (x * 57.2957795131)  // *180/pi

// Sensor variables
float accel[3];  // Actually stores the NEGATED acceleration (equals gravity, if board not moving).
float accel_min[3];
float accel_max[3];

float magnetom[3];
float magnetom_min[3];
float magnetom_max[3];
float magnetom_tmp[3];

float gyro[3];
float gyro_average[3];
int gyro_num_samples = 0;

// DCM variables
float MAG_Heading;
float Accel_Vector[3]= {0, 0, 0}; // Store the acceleration in a vector
float Gyro_Vector[3]= {0, 0, 0}; // Store the gyros turn rate in a vector
float Omega_Vector[3]= {0, 0, 0}; // Corrected Gyro_Vector data
float Omega_P[3]= {0, 0, 0}; // Omega Proportional correction
float Omega_I[3]= {0, 0, 0}; // Omega Integrator
float Omega[3]= {0, 0, 0};
float errorRollPitch[3] = {0, 0, 0};
float errorYaw[3] = {0, 0, 0};
float DCM_Matrix[3][3] = {{1, 0, 0}, {0, 1, 0}, {0, 0, 1}};
float Update_Matrix[3][3] = {{0, 1, 2}, {3, 4, 5}, {6, 7, 8}};
float Temporary_Matrix[3][3] = {{0, 0, 0}, {0, 0, 0}, {0, 0, 0}};

// Euler angles
float yaw;
float pitch;
float roll;

float yawDEG;
float pchDEG;
float rolDEG;
// DCM timing in the main loop
unsigned long timestamp;
unsigned long timestamp_old;
float G_Dt; // Integration time for DCM algorithm

// More output-state variables
boolean output_stream_on;
boolean output_single_on;
int curr_calibration_sensor = 0;
boolean reset_calibration_session_flag = true;
int num_accel_errors = 0;
int num_magn_errors = 0;
int num_gyro_errors = 0;
//blahblahblah//blahblahblah//blahblahblah
//blahblahblah//blahblahblah//blahblahblah
//blahblahblah//blahblahblah//blahblahblah
//blahblahblah//blahblahblah//blahblahblah


// Wire Slave Receiver
// by Nicholas Zambetti <http://www.zambetti.com>

// Demonstrates use of the Wire library
// Receives data as an I2C/TWI slave device
// Refer to the "Wire Master Writer" example for use with this

// Created 29 March 2006

// This example code is in the public domain.

//#include "gyroAccelerometer.h"

#include <Wire.h>
#include "pressure.h"
//#include "gyroAccelerometer.h"
//
Pressure Pressure;
//GyroAccelerometer Gyro;
String receivedString;
char tempReceive;
unsigned int WireEventCode;
unsigned int WireNextSendData;
String WireSendString;
int ParameterStack;

//I2c only sends char arrays. Therefore a data type char is included in index 0 of the array.
//It tells what kind of data was sent.
//It also serves as a buffer. 
char WireMosiType; //Holds Mosi Data Type: c_ommand or p_arameter
char WireMisoType; //Holds Miso Data Type: n_ull or i_nt or s_tring

void setup() {
  Wire.begin(8);                // join i2c bus with address #8

  //Gyro.accelSetup();
  //Gyro.updateAccelRaw();
  // Pressure Requests
  Wire.onReceive(receiveEvent); //Info is received
  Wire.onRequest(requestEvent); //Info is Requested
  Serial.begin(9600);
  old001setup();
}

void loop() {
  delay(20);
  Pressure.updatePressureSensor();
  //yprGet();
  //Serial.println(yaw);
  old001loop(); //not sure but this gives the data
}

void receiveEvent(int howMany) {
  receivedString = "";//Clear recieved string
  
  if(Wire.available()){  
    WireMosiType = Wire.read(); //Take 1 char, data type.
      while (Wire.available()) { 
        tempReceive = Wire.read(); //Receive 5 chars, data
        receivedString += tempReceive;
    }
  }
  
  WireEventCode = receivedString.toInt(); //Turn received into an int
  if(WireMosiType = 'c'){                 //treat as command if command type
    WireNextSendData = WireCallEvent(WireEventCode);
  } else if(WireMosiType = 'p') {          //store as parameter if param type
    ParameterStack = WireEventCode;
  }
}


int WireCallEvent (int EventCode){
  switch(EventCode) {
    case GET_TEMP:
      WireMisoType = 'i'; //misoType is kinda pointless, its just a buffer so the right number of chars are returned on i2c. 
                          //I can't think of any way to use it either; when master makes a request it already knows what it should be recieving.
      return Pressure.getTempTimesTen();  //Its not temp times ten anymore, its just temp. to be changed.
      break;
    case GET_PRES:
      WireMisoType = 'i';
      return Pressure.getPressure();
      break;
    case GET_DEPT:
      WireMisoType = 'i';
      return Pressure.getDepth();
      break;
    case GET_YAW:
      WireMisoType = 'f';
      return (int)yawDEG;
      break;
    case GET_PCH:
      WireMisoType = 'f';
      return (int)pchDEG;
      break;
    case GET_ROL:
      WireMisoType = 'f';
      return (int)rolDEG;
      break;
    default:
      WireMisoType = 'n';
      return 1337;        //You'll know something is wrong if you see this 1337
    break;
  }
  
}

void requestEvent() {
  WireSendString = WireMisoType + String(WireNextSendData); //padding the string with the misoType
  Wire.write(WireSendString.c_str());

}



//////////////Janky Include//////

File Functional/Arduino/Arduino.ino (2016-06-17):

#include <Servo.h>
#include "Math.h"
#include "Accelerometer.h"
#include "dataStruc.h"
//#include "QuadMotorShields.h"
#include "gyroAccelerometer.h"
#include <SoftwareSerial.h>
#include <SPI.h>
//#include "pressure.h"
#include <Wire.h>
#include "ComsMasterArd.h"
#include "VectorMotors.h"
#include "cameras.h"

//all pins used must be listed here! either as a variable to change quickly later or as a comment if it is in another file

int serialWritePin = 2; //this is the pin to control whethgeter it is recieving or sending
// SDA, SCL to Slave arduino


///// Pins used by Quad Motor Shields //////
//
// 7, 6, 11, 12, 22, 24, 31, 33, 29, 25, 27, 23, A1, 
//42, 44, 40, 24, 26, 22
//
//////////////////////////////////

///// Pins used by Pressure Sensor //////
//
//45, 50, 51, 52
//
//////////////////////////////////

//End of pin listings

///// Timers used by Quad Motor Shields on MEGA 2560//////
//
// Timer0, Timer1, Timer4
//
//////////////////////////////////

ComsMasterArd coms;
//QuadMotorShields md;//Not being used anymore
bool pressure = false;
bool voltage = false;
bool temperature = true;
bool accel = false;
bool depth = true;
bool ypr = true;

bool debug = true;

int yaw;
int pch;
int rol;
//SoftwareSerial Serial3(14, 15);
void setup() {
	Serial3.begin(9600);   //the number in here is the baud rate, it is the communication speed, this must be matched in the python
	Serial.begin(9600);     //it does not seem to work at lower baud rates 
	pinMode(serialWritePin, OUTPUT);
	pinMode(13, OUTPUT);
	pinMode(22, OUTPUT);
	pinMode(24, OUTPUT);
	digitalWrite(serialWritePin, LOW);
        motorSetup();
}

//looks cleaner than the empty while loop being everywhere in the code
void wait(){
  while(!Serial3.available())
    ;
}

//detects the start signal without accidently overshooting it because of short circuting logic
//except for input such as SSTR, that will be skipped. There should be multiple characters to 
//prevent random bytes getting past
void waitForStart(){
  while(true){
    wait();
    if('S' == Serial3.read()){
      wait();
      if('T' == Serial3.read()){
        wait();
        if('R' == Serial3.read()){
          break;
        }
      }
    }
  }
}

Input readBuffer() {  
        Input input;
        wait();//makes sure that a byte of data is not missed 
        input.buttons1 = Serial3.read();
        wait();
        input.buttons2 = Serial3.read();
        wait();
        input.primaryX = Serial3.parseInt();
        Serial3.read();
        wait();
        input.primaryY = Serial3.parseInt();
        Serial3.read();
        wait();
        input.secondaryX = Serial3.parseInt();
        Serial3.read();
        wait();
        input.secondaryY = Serial3.parseInt();
        Serial3.read();
        wait();
        input.triggers = Serial3.parseInt();
        Serial3.read();
        return input;
}
void processInput(Input i){
  /*
    if((CHECK_BIT(i.buttons1, 2))){digitalWrite(22, HIGH);}
        else {digitalWrite(22, LOW);}
    if((CHECK_BIT(i.buttons1, 2))){digitalWrite(24, LOW);}
        else {digitalWrite(24, HIGH);}
    */
  setCameras(i.buttons1);
  setMotors(i.primaryX, i.primaryY, i.triggers, i.secondaryX,i.buttons1);
}

void writeToCommand(Input i){
  Serial3.print("STR");
  int lines = 0;
  if (pressure) lines += 2;
  if (voltage) lines += 2;
  if (temperature) lines += 2;
  if (depth) lines += 2;
  if (accel) lines += 4;
  if (ypr) lines += 6;
  String numberOfLines = String(lines);
  int counter = 0;
  while ((counter + numberOfLines.length()) != 3) {
	  Serial3.print("0");
	  counter++;
  }
  Serial3.print(numberOfLines); //print the number of lines of input the python program can read in three digits
  if (pressure) {
	  Serial3.println("PSR"); //tell it the next line is Pressure
    coms.sendSlaveCmd(GET_PRES);
	  Serial3.println(coms.getSlaveData());
  }
  if (voltage) {
	  Serial3.println("VLT"); //tell it the next line is Power info
	  Serial3.println( (((float)(analogRead(A1))*(5.0/1023.0))-2.52)   /.066 );
  }
  if (temperature) {
	  Serial3.println("TMP"); //tell it the next line is Temperature
    coms.sendSlaveCmd(GET_TEMP);
	  Serial3.println((float)analogRead(A0)/(2.048)-273.15);
	  //Serial3.print(coms.getSlaveData());
  }
  if (ypr) {
    
    coms.sendSlaveCmd(GET_YAW);
    Serial3.println("YAW");
    Serial3.println(coms.getSlaveData());
    //Serial3.println(coms.getSlaveData());
    
    coms.sendSlaveCmd(GET_PCH);
    Serial3.println("PCH");
    Serial3.println(coms.getSlaveData());
    
    coms.sendSlaveCmd(GET_ROL);
    Serial3.println("ROL");
    Serial3.println(coms.getSlaveData());


    if(debug){
      
    coms.sendSlaveCmd(GET_YAW);
    Serial.println("YAW");
    yaw = coms.getSlaveData();
    
    Serial.println(yaw);
    //Serial3.println(coms.getSlaveData());
    
    coms.sendSlaveCmd(GET_PCH);
    Serial.println("PCH");
    Serial.println(coms.getSlaveData());
    
    coms.sendSlaveCmd(GET_ROL);
    Serial.println("ROL");
    Serial.println(coms.getSlaveData());
    
    }
  }
  if (depth) {
	  Serial3.println("DPT"); //tell it the next line is Depth
    coms.sendSlaveCmd(GET_DEPT);
	  Serial3.println(coms.getSlaveData());
  }
}
void debugInput(Input i){
  //the following is for debugging, prints all input back out on the serial used for programming the arduino
  Serial.print("buttons: ");
  Serial.print(i.buttons2);
  Serial.print(" ");
  Serial.print(i.buttons1);
  Serial.print(" X1: ");
  Serial.print(i.primaryX);
  Serial.print(" Y1: ");
  Serial.print(i.primaryY);
  Serial.print(" X2: ");
  Serial.print(i.secondaryX);
  Serial.print(" Y2: ");
  Serial.print(i.secondaryY);
  Serial.print(" Trig: ");
  Serial.println(i.triggers);

}
void loop() { 
     if (Serial3.available()) {
		 //digitalWrite(13, HIGH);
        waitForStart();
        Input i = readBuffer();
        digitalWrite(serialWritePin, HIGH);
        if(debug==true)debugInput(i);
        writeToCommand(i); //this is where the code to write back to topside goes.
		Serial3.flush();
        delay(50);         //this delay allows for hardware serial to work with rs485
        digitalWrite(serialWritePin, LOW);
        
        processInput(i);//gives the inputs to the motors
    }
}

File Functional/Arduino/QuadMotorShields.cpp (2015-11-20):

#include "QuadMotorShields.h"

// Constructors ////////////////////////////////////////////////////////////////



QuadMotorShields::QuadMotorShields()
{
  //Pin map, Bottom Pololu (yellow) IGNORE COLORS THEY LIE NOW!
  _INA1 = 31; // M1INA
  _INB1 = 33; // M1INB
  _EN1DIAG1 = 29; // M1EN
  _CS1 =A0;  //M1CS
  _INA2 = 25;   //M2INA2
  _INB2 = 27;   //M2INB2
  _EN2DIAG2 = 23; //M2EN
  _CS2 = A1; //M2CS

  //Pin map, Top Pololu (pink)
  _INA3 = 42; // M1INA //ORIGINALLY 30
  _INB3 = 44; // M1INB  //ORIGINALLY 32
  _EN3DIAG3 = 40; // M1EN //ORIGINALLY 28
  _INA4 = 24; //M2INA2,Blue
  _INB4 = 26; //M2INB2,Red
  _EN4DIAG4 = 22; //M2EN, Brown 

}

QuadMotorShields::QuadMotorShields(unsigned char INA1, unsigned char INB1, unsigned char EN1DIAG1, unsigned char CS1, 
                                               unsigned char INA2, unsigned char INB2, unsigned char EN2DIAG2, unsigned char CS2,
											   unsigned char INA3, unsigned char INB3, unsigned char EN3DIAG3,  
											   unsigned char INA4, unsigned char INB4, unsigned char EN4DIAG4)
{
  //Pin map
  //PWM1 and PWM2 cannot be remapped because the library assumes PWM is on timer1
  _INA1 = INA1;
  _INB1 = INB1;
  _EN1DIAG1 = EN1DIAG1;
  _CS1 = CS1;
  _INA2 = INA2;
  _INB2 = INB2;
  _EN2DIAG2 = EN2DIAG2;
  _CS2 = CS2;

  //2nd set of motors ~ custom mapping
  _INA3 = INA4; // originally INA3, but the motor is being a little bitch
  _INB3 = INB4; // originally INB3
  _EN3DIAG3 = EN3DIAG3;
  _INA4 = INA4;
  _INB4 = INB4;
  _EN4DIAG4 = EN4DIAG4;
}

// Public Methods //////////////////////////////////////////////////////////////
void QuadMotorShields::init()
{
// Define pinMode for the pins and set the frequency for timer1.

  pinMode(_INA1,OUTPUT);
  pinMode(_INB1,OUTPUT);
  pinMode(_PWM1,OUTPUT);
  pinMode(_EN1DIAG1,INPUT);
  pinMode(_CS1,INPUT);
  pinMode(_INA2,OUTPUT);
  pinMode(_INB2,OUTPUT);
  pinMode(_PWM2,OUTPUT);
  pinMode(_EN2DIAG2,INPUT);
  pinMode(_CS2,INPUT);
  pinMode(_INA3, OUTPUT);
  pinMode(_INB3, OUTPUT);
  pinMode(_PWM3, OUTPUT);
  pinMode(_EN3DIAG3, INPUT);
  pinMode(_INA4, OUTPUT);
  pinMode(_INB4, OUTPUT);
  pinMode(_EN4DIAG4, INPUT);
  //#if defined(__AVR_ATmega168__)|| defined(__AVR_ATmega328P__) || defined(__AVR_ATmega32U4__)
  // Timer 1 configuration
  // prescaler: clockI/O / 1
  // outputs enabled
  // phase-correct PWM
  // top of 400
  //
  // PWM frequency calculation
  // 16MHz / 1 (prescaler) / 2 (phase-correct) / 400 (top) = 20kHz
  //TCCR1A = 0b10100000;
  //TCCR1B = 0b00010001;
  //ICR1 = 400;

  //TCCR3A = 0b10100000;
  //TCCR3B = 0b00010001;
  //ICR3 = 400;

  //#endif
}
// Set speed for motor 1, speed is a number betwenn -400 and 400
void QuadMotorShields::setM1Speed(int speed)
{
  unsigned char reverse = 0;
  
  if (speed < 0)
  {
    speed = -speed;  // Make speed a positive quantity
    reverse = 1;  // Preserve the direction
  }
  if (speed > 400)  // Max PWM dutycycle
    speed = 400;
  #if defined(__AVR_ATmega168__)|| defined(__AVR_ATmega328P__) || defined(__AVR_ATmega32U4__)
  OCR1A = speed;
  #else
  analogWrite(_PWM1,speed * 51 / 80); // default to using analogWrite, mapping 400 to 255
  #endif
  if (speed == 0)
  {
    digitalWrite(_INA1,LOW);   // Make the motor coast no
    digitalWrite(_INB1,LOW);   // matter which direction it is spinning.
  }
  else if (reverse)
  {
    digitalWrite(_INA1,LOW);
    digitalWrite(_INB1,HIGH);
  }
  else
  {
    digitalWrite(_INA1,HIGH);
    digitalWrite(_INB1,LOW);
  }
}

// Set speed for motor 2, speed is a number betwenn -400 and 400
void QuadMotorShields::setM2Speed(int speed)
{
  unsigned char reverse = 0;
  
  if (speed < 0)
  {
    speed = -speed;  // make speed a positive quantity
    reverse = 1;  // preserve the direction
  }
  if (speed > 400)  // Max 
    speed = 400;
  #if defined(__AVR_ATmega168__)|| defined(__AVR_ATmega328P__) || defined(__AVR_ATmega32U4__)
  OCR1B = speed;
  #else
  analogWrite(_PWM2,speed * 51 / 80); // default to using analogWrite, mapping 400 to 255
  #endif 
  if (speed == 0)
  {
    digitalWrite(_INA2,LOW);   // Make the motor coast no
    digitalWrite(_INB2,LOW);   // matter which direction it is spinning.
  }
  else if (reverse)
  {
    digitalWrite(_INA2,LOW);
    digitalWrite(_INB2,HIGH);
  }
  else
  {
    digitalWrite(_INA2,HIGH);
    digitalWrite(_INB2,LOW);
  }
}
// Set speed for motor 3, speed is a number between -400 and 400
void QuadMotorShields::setM3Speed(int speed)
{
	unsigned char reverse = 0;

	if (speed < 0)
	{
		speed = -speed;  // Make speed a positive quantity
		reverse = 1;  // Preserve the direction
	}
	if (speed > 400)  // Max PWM dutycycle
		speed = 400;
#if defined(__AVR_ATmega168__)|| defined(__AVR_ATmega328P__) || defined(__AVR_ATmega32U4__)
	OCRA = speed;
#else
	analogWrite(_PWM3, speed * 51 / 80); // default to using analogWrite, mapping 400 to 255
#endif
	if (speed == 0)
	{
		digitalWrite(_INA3, LOW);   // Make the motor coast no
		digitalWrite(_INB3, LOW);   // matter which direction it is spinning.
	}
	else if (reverse)
	{
		digitalWrite(_INA3, LOW);
		digitalWrite(_INB3, HIGH);
	}
	else
	{
		digitalWrite(_INA3, HIGH);
		digitalWrite(_INB3, LOW);
	}
}
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

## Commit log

2015-10-05 Readme
    Added real readme file… more to be added later
2015-10-05 Updated code to control the motors of Santiago and to function on the Arduino Mega with 3 serial ports
2015-10-05 Added instructions for installing current dependiencies
2015-10-05 Added new folders
    Each new folder has a readme file for use to share notes in. When you
    guys start trying new sensors on your Arduino UNOs put the code in
    these. We can merge them with the core code of the Arduino mega later.
2015-10-10 Added Power Monitor for measuring Voltage stepped down from 48 V. - Anuj
2015-10-10 Create PressureSensorHardCoded
    Using the data sheet, hard coded the values.
2015-10-14 fixed waitForStart to wait for a start signal
    [sketch_sep29a.ino]
2015-10-16 improved the communication code for the gui, fixed issue with double blocking by adding timeout to reads
    [controller.py, main.py, twoWayCom.ino]
2015-10-17 Create MS5541_Oct17_Working
    MS5541 Arduino, functional pressure and temperature sensor
    to do maybe:
    modulize
    callibrate
    waterproof
2015-10-20 Fixed two way rs485 communication on serial ports.
    [main.py, twoWayCom.ino]
2015-10-21 Added stepper motor resources
    Hopefully this helps. Stepper motors will be useful for external tools
    on the bot.
2015-10-25 fixed pin and clock issues for the pressure sensor
    [pressure.cpp]
2015-10-25 Oct 24 Update
    Added useful comments and links in stepper motors and TwoWayCom
2015-10-25 updated pin reference in Arduino.ino and and condensed input debugging
2015-10-25 updated pins to match mega rather than uno for the pressure.cpp
2015-10-26 Comments
    Comments updated for current sense
2015-10-26 Revert "fix merge?"
    This reverts commit e8da7b3eed5a88db991e8e0ecd1c7a0840162b99.
    [main.py]
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2015-10-29 Create TimedInterrupt_Example
    Read comments at beginning.
    This file is just an example of timer interrupt function
2015-10-30 Update TimedInterrupt_Example
    Working but stepper motor driver might be burned out.
    (inputs are good, smoke did not come out, but the 4 output wires that go to the stepper motor are not good. They stay at 8v and 0v
2015-10-31 Update and rename TimedInterrupt_Example to StepperMotor_Oct31
    Includes Timed Interrupting Stepper Motor, Timer 1 and Timer 2.
    Has input parameters
    Second half of intro comment section is outdated
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2015-10-31 Update and rename Stepper_Motor_Oct24 to stepperMotor_cpp
    Use this as cpp
2015-10-31 Create stepperMotor_h
    use as .h
    4 functions:
    two for setting pins
    two for driving the stepper motor
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2015-10-31 Update and rename StepperMotor_Oct31 to StepperMotor_TestFile_ino
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2015-11-01 Update stepperMotor_h
    commented on some things I can add.
    ("Eric's To Do List")
2015-11-02 Update stepperMotor_h
    lines 11 through 56 are a summary of how I tested the run time of ISR.
    Conclusion starts line 41.
    Theoretically, each interrupt will take up to 8us.
    At a realistic speed of 30degrees/second, running the stepper motor slows other processes by 0.026667%.
    Extreme case: When microstepping at 1/16 steps and still going 30 degrees/second, running the stepper motor slows other processes by 0.4266667%
2015-11-06 Edits on old quad motors.cpp
    No real changes
2015-11-07 added accelerometer raw data.
2015-11-07 fixed some pressure sensor things.
    [Arduino.ino, pressure.cpp]
2015-11-12 Added motor testing code and the start of Accel code
2015-11-12 Pin changes
    Saves a few timers
2015-11-12 Pin changes
    Corresponding library changes. Checked and still works on Santiago.
2015-11-12 added wiring stuff
    [UROV 2016 wiring.fzz]
2015-11-12 Wiring progress
    Wiring diagram in Fritzing has all basic parts except DC DC converter.
    ESCs are represented by servos because they use PWM, power to them will
    be implied for now.
    [UROV 2016 wiring.fzz]
2015-11-14 Wiring updates
    [UROV 2016 wiring.fzz]
2015-11-14 Update pressure.cpp
    The Pressure Constructor made the arduino not do anything. After removing/adding each function in the constructor, i determined it was delay(100); that caused the problem. I have no idea why this is the case.
    Changes: Removed Delay(100).
    [pressure.cpp]
2015-11-17 Update ComsMasterArd.ino
    masterWrite now takes 1 parameter, WireEventCode, which is an int.
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2015-11-21 Added some power board stuffs
    [Power Board.fzz]
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2015-11-23 Made camera library
    I think the bit-shifting trick will work on pin assignments… otherwise
    delete three lines and uncomment the big block in camera.cpp
2016-01-23 Update to include brownout prevention function in vector motors.cpp
    read title
    [VectorMotors.cpp]
2016-01-23 Added current readings
    “Voltage” spot now shows how many amps go through the whole system @48
    volts. Multiply by 4 for 12V amperage
2016-02-07 Testing camera relays
    pin 13 toggles camera output relay
2016-02-16 Added Camera Switching Beta
    Works with pins 22 and 24.
2016-02-16 Added PCB directory starting point
    This has the power board. Josh will put his eagle files in the
    designated folder.
    [Power Supply Board.brd, Power Supply Board.sch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]
2016-02-20 YPR stuff
    YPR on slave should be functional
    YPR -> slave -> master -> serial3
    master will print ypr to serial3
2016-02-20 bugfixes
    coms now has properly matching data in case statement
    sampling rate to 50Hz (1/20ms)
    [ComsSlaveArd.ino]
2016-02-27 Functional Artificial Horizon
    Artificial horizon now takes arduino's output
2016-02-27 YPR stuff
    Slave cases changes to #defines
    master sends data that luka has successfully received
    Some strange error was fixed by plugging the slave to computer, clearing
    its serial from something not sure why. This is no longer an issue.
    [Arduino.ino, ComsSlaveArd.ino]
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2016-03-31 Updated Pins
    Named every pin on MAX485 and Multiplexer
    [UROV 2016 wiring.fzz]
2016-03-31 Schematic and Breadboard Update
    Organized the schematic and attached a few pins. This is my version to
    avoid any weird merges.
    [UROV 2016 Sam_wiring.fzz]
2016-04-02 MotorLimits & Rotations
    Added Rotations
    Cleaned up some of code for limiting motor to +-400
2016-04-02 Improved Artificial Horizon
    Improved artificial horizon, and added amps for each motor.
2016-04-09 Fixed UI connection issue
    [main.py]
2016-04-09 Fixed bug in code
    [ComsSlaveArd.ino]
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2016-04-10 Some vector driving fixes
    [VectorMotors.cpp]
2016-04-23 Created low pass filter for sensor data
    Created low pass filter for sensor data
2016-04-23 Improved efficiency and and improved A.H.
    Improved efficiency by deleting unnecessary fucntion and importing less
    stuff and improved A.H. by adding 5 point filter.
2016-05-26 Inproments to the UI
    Added half power mode, improved AH filter, organized code and added
    comments.
2016-05-28 Removed Labels on Arduino's communication
    Removed Labels on Arduino's communication
2016-06-17 Improved UI
    Added crash reports and the ability to receive motor info.
    [main.py]
2016-10-22 Added reading funcs and fixed Serial Finder
    Added reading funcs to make code concise and fixed Serial Finder so it
    doesn't crash when a serial devise is not connected
    [controller.py, main.py]
